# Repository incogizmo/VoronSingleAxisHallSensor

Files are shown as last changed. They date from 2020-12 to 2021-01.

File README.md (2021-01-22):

# Single Axis Hall Sensor for Voron
This is a hall effect sensor based of the existing Voron hall effect sensor for Voron v2.
Designed to be a single axis only and fit within the Y endstop area of V1.8 and be small enough to be flexible for mounting options for X axis.

This branch is the Normally Open variant of the board. This does not provide failsafe if the sensor / wiring fail.

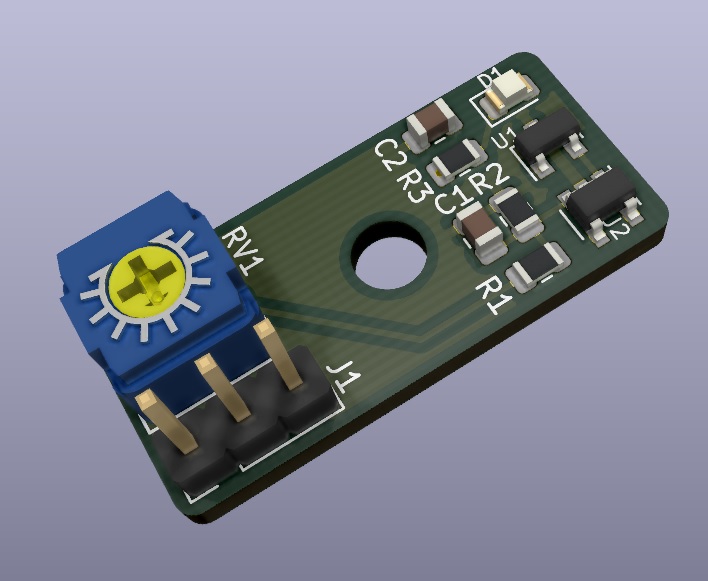
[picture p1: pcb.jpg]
PCB


This is designed for use with Voron v1.8 printer: https://github.com/VoronDesign/ http://vorondesign.com/

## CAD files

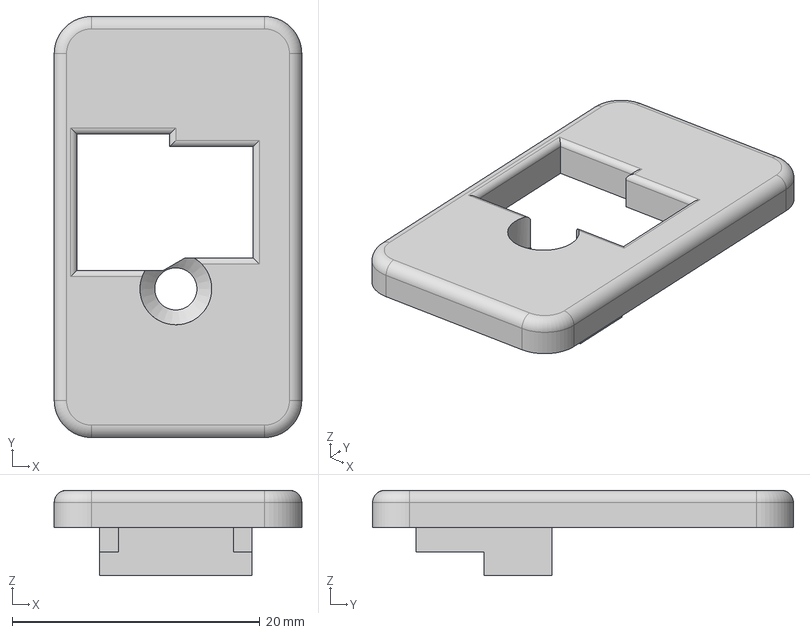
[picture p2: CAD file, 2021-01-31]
Voron1.8STLs/y_hall_sensor_mount_lid.step
20.0 x 34.0 x 6.90 mm

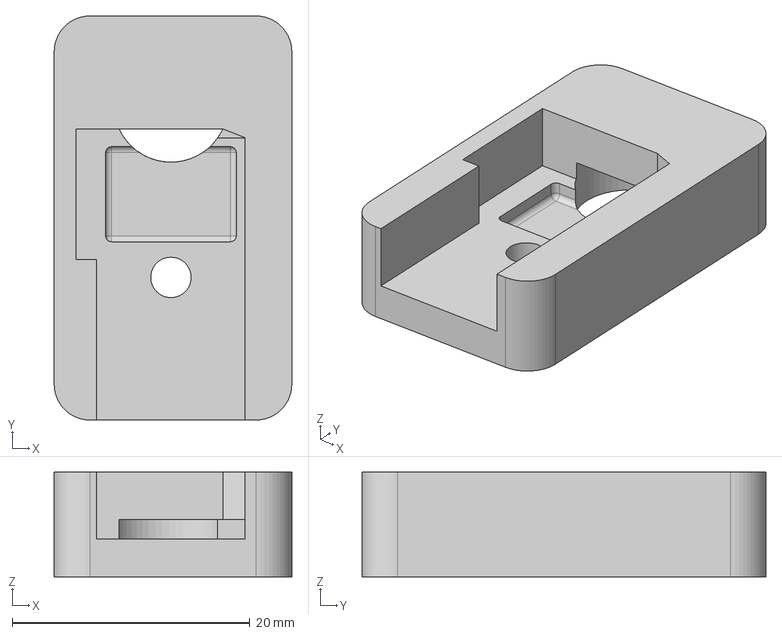
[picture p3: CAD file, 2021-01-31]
Voron1.8STLs/y_hall_sensor_mount.step
20.0 x 34.0 x 8.80 mm

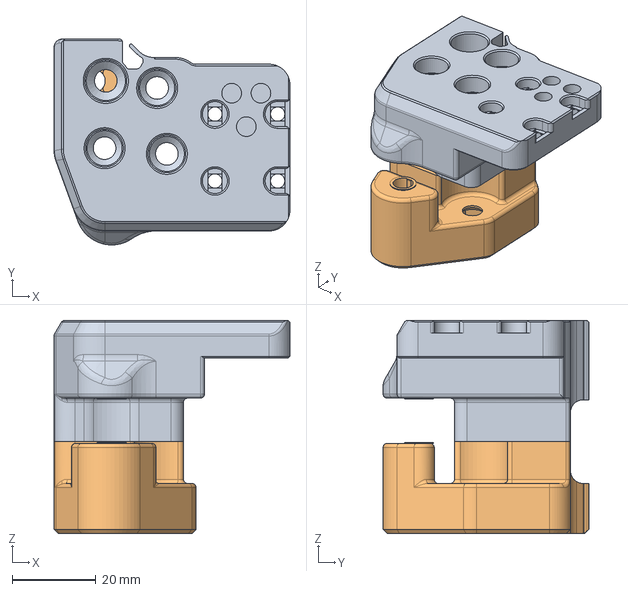
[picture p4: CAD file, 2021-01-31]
Voron1.8STLs/xy_joint_right.step
56.5 x 49.2 x 51.0 mm

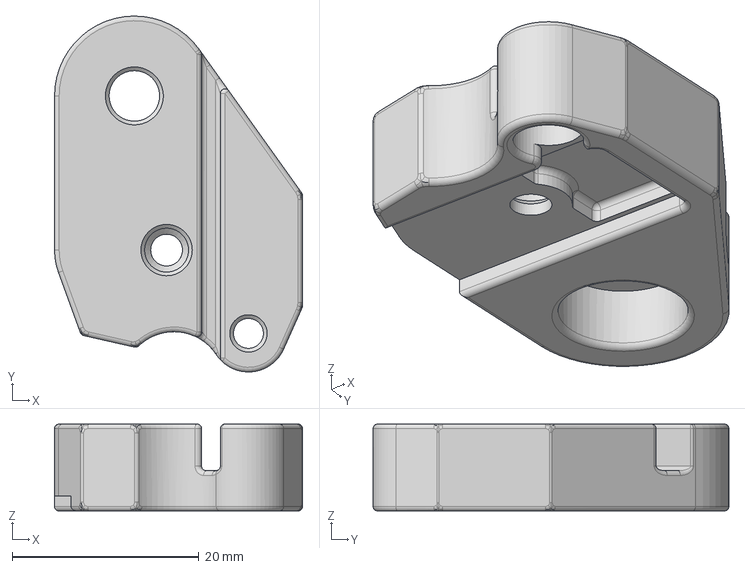
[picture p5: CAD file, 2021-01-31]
Voron1.8STLs/x_hall_sensor_mount.step
26.6 x 38.1 x 9.31 mm

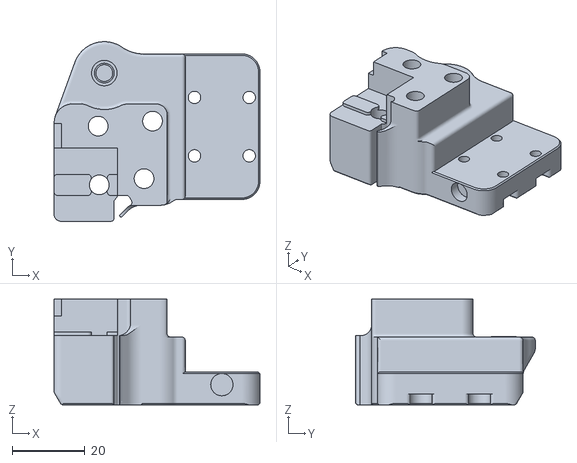
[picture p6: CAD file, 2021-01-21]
Voron1.8STLs/xy_joint_right_upper.stl
56.5 x 49.2 x 29.0

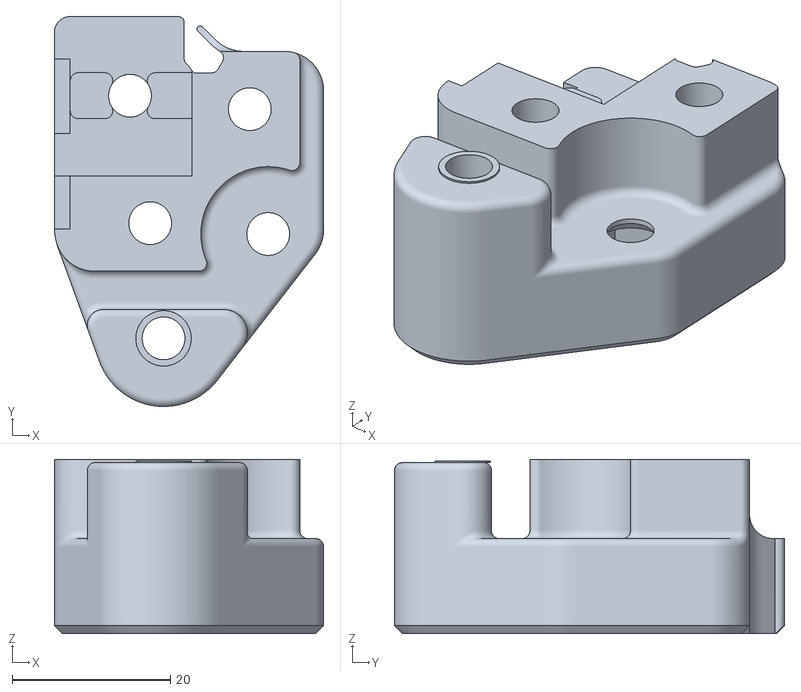
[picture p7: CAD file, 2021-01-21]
Voron1.8STLs/xy_joint_right_lower.stl
34.0 x 49.2 x 22.0

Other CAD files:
Voron1.8STLs/x_hall_sensor_mount.stl
Voron1.8STLs/y_hall_sensor_mount.stl
Voron1.8STLs/y_hall_sensor_mount_lid.stl

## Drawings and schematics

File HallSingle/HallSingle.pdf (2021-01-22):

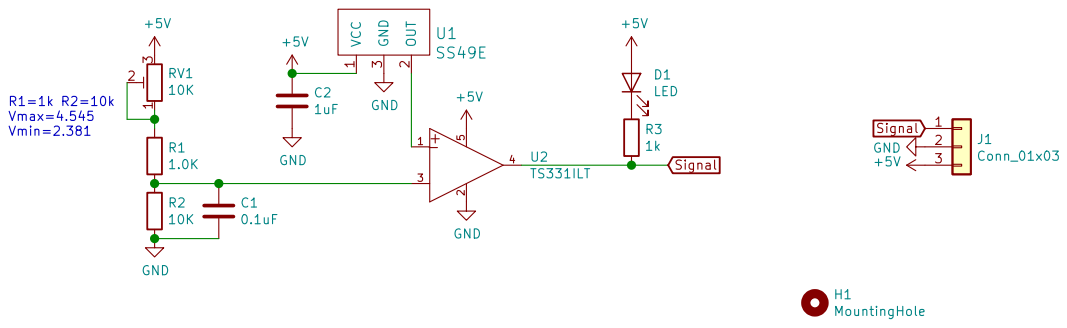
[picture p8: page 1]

File: HallSingle.sch Sheet: /
Id: 1/1 Title:

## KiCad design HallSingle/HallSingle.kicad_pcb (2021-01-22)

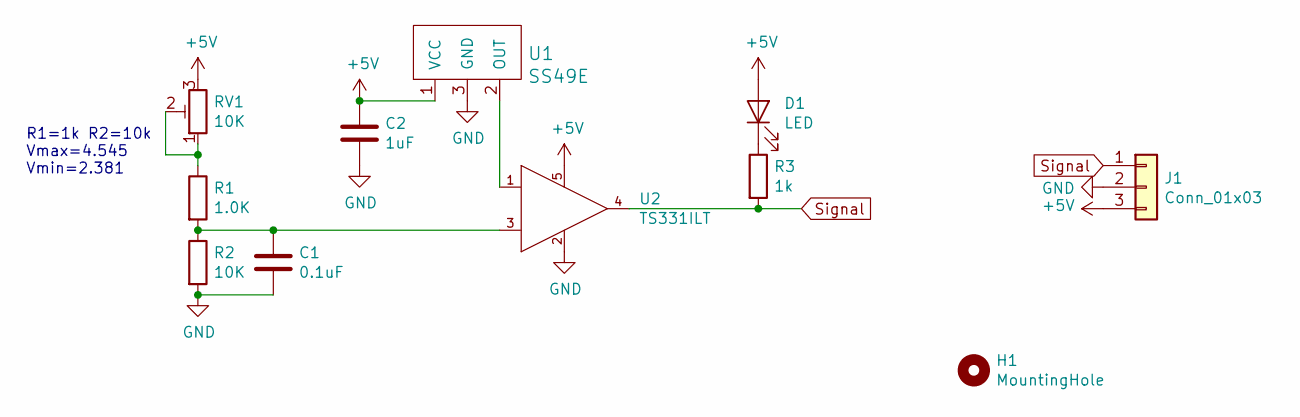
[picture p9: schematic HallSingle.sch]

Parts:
C1: 0.1uF; C_0805_2012Metric
C2: 1uF; C_0805_2012Metric
D1: LED; LED_0805_2012Metric
H1: MountingHole; MountingHole_3.2mm_M3
J1: Conn_01x03; PinHeader_1x03_P2.54mm_Vertical
R1: 1.0K; R_0805_2012Metric
R2: 10K; R_0805_2012Metric
R3: 1k; R_0805_2012Metric
RV1: 10K; CT6EP103
U1: SS49E; SOT-23
U2: TS331ILT; SOT-23-5; mouser part number 511-TS331ILT; digikey description IC COMPARATOR SINGLE SOT23-5

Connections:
+5V: C2.1, D1.2 (A), J1.3, RV1.3, U1.1 (VCC), U2.5 (VCC+)
GND: C1.2, C2.2, J1.2, R2.2, U1.3 (GND), U2.2 (VCC-)
unnamed: C1.1, R1.2, R2.1, U2.3 (IN-)
unnamed: D1.1 (K), R3.1
unnamed: R1.1, RV1.1, RV1.2
unnamed: U1.2 (OUT), U2.1 (IN+)
Signal: J1.1, R3.2, U2.4 (OUT)

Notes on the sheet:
R1=1k R2=10k Vmax=4.545 Vmin=2.381

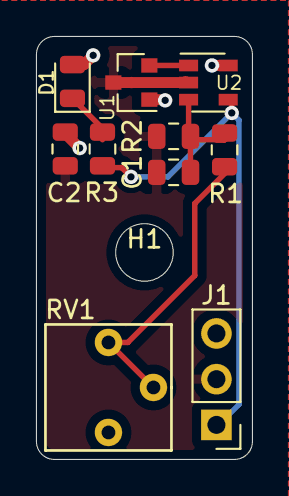
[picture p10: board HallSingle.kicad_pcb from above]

Board: 2 copper layers, 12.0 x 23.5 mm, 11 parts (0 on the bottom side), 7 nets.

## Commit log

2020-12-30 initial import
    [HallSingle-B_Cu.gbr, HallSingle-B_Mask.gbr, HallSingle-B_Paste.gbr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]
2020-12-30 Added PCB jpeg
2020-12-30 Added Voron Logo and filled missing resistor value
    [HallSingle.kicad_pcb, HallSingle.sch]
2020-12-30 Reduced total length 1mm to remove interferance with M5 in V1.8 Y mount
    [HallSingle.kicad_pcb]
2020-12-30 fixed missed trace
    [HallSingle.kicad_pcb]
2020-12-30 Reduced size due to almost certain interferance from screw heads on v1.8 Y.
    [HallSingle.kicad_pcb, HallSingle.sch]
2020-12-30 actually reduce the pcb size this time....
    [HallSingle.kicad_pcb]
2021-01-02 Fixed Mounting hole
    [HallSingle-B_Cu.gbr, HallSingle-B_Mask.gbr, HallSingle-B_Paste.gbr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]
2021-01-02 Remove JLC - doesnt fit with required sizing
    [HallSingle.kicad_pcb]
2021-01-19 merged autosave with prod pcb
2021-01-21 Updated with revision number. Corrected header orientation. added ibom
    [HallSingle.kicad_pcb, HallSingle.sch]
2021-01-21 Forgot the gerbers
    [HallSingle-B_Cu.gbr, HallSingle-B_Mask.gbr, HallSingle-B_Paste.gbr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]
2021-01-21 removed gerber.zip (incorrect version)
2021-01-21 Added STLs for Voron 1.8
    [x_hall_sensor_mount.stl, xy_joint_right_lower.stl, xy_joint_right_upper.stl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]
2021-01-22 added ibom and other small fixes
    [HallSingle.kicad_pcb]
2021-01-31 Added step files.
    [x_hall_sensor_mount.step, xy_joint_right.step, y_hall_sensor_mount.step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]
